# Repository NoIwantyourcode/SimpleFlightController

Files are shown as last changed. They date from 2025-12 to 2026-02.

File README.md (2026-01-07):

# Introduction
Hi!,

Welcome to my simple filght controller repository

This is a flight controller as the name suggests that is specifically designed to pilot remote controlled aircraft and provides accurate data to make flying your plane easier!,
some features I plan for to be included in the firmware are
       - 3 axis stabilization
       - altitude management

This is not a comprehensize list of features I may include and the actual firmware may have a lot more

Here are a few images of the Flight controller Schematics, PCB view and Rendered PCB view

# Schematics



# PCB view



# Rendered PCB View




# Display case (one screenshot is fitted with PCB)




NOTES TO REVIEWER:

I have had to substitute a few of components due to part shortfalls like the ICM-45686 had to substituted with the ICM-45605

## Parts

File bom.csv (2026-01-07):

Your BOM |  |  | Order Information
Component | Comment | Footprint | JLCPCB Part # | Product link | Lib Type | Qty | Source | Total Price ($)
Capacitor | 1uF | 0402 | C52923 | https://jlcpcb.com/partdetail/53938-CL05A105KA5NQNC/C52923 | Basic | 20 | 20 JLCPCB | 0.06
Capacitor | 10uF | 0402 | C15525 | https://jlcpcb.com/partdetail/16204-CL05A106MQ5NUNC/C15525 | Basic | 20 | 20 JLCPCB | 0.088
Capacitor | 44uF | 0805 | C16780 | https://jlcpcb.com/partdetail/17464-CL21A476MQYNNNE/C16780 | Basic | 8 | 8 JLCPCB | 0.2288
Capacitor | 47nF | 0201 | C505465 | https://jlcpcb.com/partdetail/YAGEO-CC0201KRX5R7BB473/C505465 | Extended | 20 | 20 JLCPCB | 0.056
Capacitor | 10uF | 0805 | C440198 | https://jlcpcb.com/partdetail/439567-GRM21BR61H106KE43L/C440198 | Basic | 8 | 8 JLCPCB | 0.4968
Capacitor | 10uF | 0603 | C19702 | https://jlcpcb.com/partdetail/20411-CL10A106KP8NNNC/C19702 | Basic | 20 | 20 JLCPCB | 0.116
Capacitor | 22uF | 0805 | C45783 | https://jlcpcb.com/partdetail/46786-CL21A226MAQNNNE/C45783 | Basic | 20 | 20 JLCPCB | 0.476
Capacitor | 100nF | 0201 | C76934 | https://jlcpcb.com/partdetail/MurataElectronics-GRM033R61A104KE15D/C76934 | Extended | 36 | 36 JLCPCB | 0.0432
Capacitor | 2.2uF | 0603 | C23630 | https://jlcpcb.com/partdetail/24366-CL10A225KO8NNNC/C23630 | Basic | 20 | 20 JLCPCB | 0.112
Capacitor | 22uF | 0402 | C415703 | https://jlcpcb.com/partdetail/408393-GRM155R60J226ME11D/C415703 | Extended | 8 | 8 JLCPCB | 0.2704
Capacitor | 20pF | 0201 | C76923 | https://jlcpcb.com/partdetail/MurataElectronics-GRM0335C1H200JA01D/C76923 | Extended | 20 | 20 JLCPCB | 0.05
Capacitor | 6.8pF | 0201 | C85916 | https://jlcpcb.com/partdetail/MurataElectronics-GRM0335C1H6R8CA01D/C85916 | Extended | 20 | 20 JLCPCB | 0.038
Capacitor | 2.2uF | 0201 | C319184 | https://jlcpcb.com/partdetail/300450-GRM033R61A225ME47D/C319184 | Extended | 20 | 20 JLCPCB | 0.204
MicroSD card | TF-01A | TF-SMD_TF-01A | C91145 | https://jlcpcb.com/partdetail/Korean_HropartsElec-TF01A/C91145 | Extended | 2 | 2 JLCPCB | 0.3512
LED | LED | 0402 | C965793 | https://jlcpcb.com/partdetail/XINGLIGHT-XL1005UGC/C965793 | Extended | 20 | 20 JLCPCB | 0.152
Battery terminal | Screw_Terminal_01x02 | TerminalBlock_Xinya_XY308-2.54-2P_1x02_P2.54mm_Horizontal | C557685 | https://jlcpcb.com/partdetail/Ningbo_Xinlaiya_Elec-XY308_2_542P/C557685 | Extended | 2 | 2 JLCPCB | 0.4658
Servo pin headers | Conn_01x03 | PinHeader_1x03_P2.54mm_Vertical | C49257 | https://jlcpcb.com/partdetail/50265-2_54_1_3P/C49257 | Extended | 10 | 10 JLCPCB | 0.169
Inductors | 1uH | L2520 | C435392 | https://jlcpcb.com/partdetail/MurataElectronics-DFE252012F_1R0MP2/C435392 | Extended | 5 | 5 JLCPCB | 0.5115
Inductors | 1.5uH | IND-SMD_L4.0-W4.0-A | C7417180 | https://jlcpcb.com/partdetail/Coilcraft-XGL4020152MEC/C7417180 | Extended | 2 | 2 JLCPCB | 2.66
Inductors | 5.6uH | IND-SMD_L3.0-W3.0 | C5120864 | https://jlcpcb.com/partdetail/CENKER-CKCS3015_5_6uHM/C5120864 | Extended | 15 | 15 JLCPCB | 0.489
Inductors | FCM1608KF-601T03 | L0603 | C141723 | https://jlcpcb.com/partdetail/TAITECH-FCM1608KF601T03/C141723 | Extended | 20 | 20 JLCPCB | 0.094
Resistors | 5.1K | 0201 | C270344 | https://jlcpcb.com/partdetail/259874-0201WMF5101TEE/C270344 | Extended | 20 | 20 JLCPCB | 0.016
Resistors | 5.23K | 0201 | C332546 | https://jlcpcb.com/partdetail/RALEC-RTT015231FTH/C332546 | Extended | 20 | 20 JLCPCB | 0.02
Resistors | 30.1K | 0201 | C273278 | https://jlcpcb.com/partdetail/YAGEO-RC0201FR0730K1L/C273278 | Extended | 20 | 20 JLCPCB | 0.02
Resistors | 383 | 0201 | C423551 | https://jlcpcb.com/partdetail/416501-0201WMF3830TEE/C423551 | Extended | 20 | 20 JLCPCB | 0.01
Resistors | 10K | 0201 | C7467266 | https://jlcpcb.com/partdetail/FOJAN-FRC0201J103TS/C7467266 | Extended | 40 | 40 JLCPCB | 0.024
Resistors | 100K | 0402 | C25741 | https://jlcpcb.com/partdetail/26484-0402WGF1003TCE/C25741 | Basic | 20 | 20 JLCPCB | 0.012
Resistors | 22.1K | 0201 | C423662 | https://jlcpcb.com/partdetail/416612-0201WMF2212TEE/C423662 | Extended | 20 | 20 JLCPCB | 0.016
Boot and Reset switch | TS-1088-AR02016 | SW-SMD_L3.9-W3.0-P4.45 | C720477 | https://jlcpcb.com/partdetail/XUNPU-TS_1088AR02016/C720477 | Basic | 8 | 8 JLCPCB | 0.3544
STM32 Chip | STM32F722RETx | LQFP-64_10x10mm_P0.5mm | C118207 | https://jlcpcb.com/partdetail/STMicroelectronics-STM32F722RET6/C118207 | Extended | 2 | 2 JLCPCB | 10.3024
Battery management IC | BQ25883RGER | VFQFPN-24_L4.0-W4.0-P0.50-BL-EP2.8 | C544362 | https://jlcpcb.com/partdetail/TexasInstruments-BQ25883RGER/C544362 | Extended | 2 | 2 JLCPCB | 9.4208
Barometric Sensor | BMP580 | LGA-10_L2.0-W2.0-P0.50-TL_BMP580 | C22391138 | https://jlcpcb.com/partdetail/BoschSensortec-BMP580/C22391138 | Extended | 2 | 2 JLCPCB | 2.1662
Buck Boost Converter | TPS63070RNMR | VQFN-HR-15_L3.0-W2.5-P0.50-BL_TPS63070RNMR | C2071354 | https://jlcpcb.com/partdetail/TexasInstruments-TPS630702RNMR/C2071354 | Extended | 2 | 2 JLCPCB | 3.432
Buck Boost converter | LMR51430 | SOT-23-6 | C5219261 | https://jlcpcb.com/partdetail/TexasInstruments-LMR51430YFDDCR/C5219261 | Extended | 2 | 2 JLCPCB | 1.813
Inertial Measurement Unit | ICM-45686 | LGA-14_L3.0-W2.5-P0.50-TL | C38673635 | https://jlcpcb.com/partdetail/TDKInvenSense-ICM45605/C38673635 | Extended | 2 | 2 JLCPCB | 14.2938
Type C port | TYPE-C16PIN2MD(073) | USB-C-SMD_TYPE-C-6PIN-2MD-073 | C2765186 | https://jlcpcb.com/partdetail/SHOUHAN-TYPE_C_16PIN_2MD_073/C2765186 | Extended | 3 | 3 JLCPCB | 0.189
Crystal | X322525MOB4SI | CRYSTAL-SMD_4P-L3.2-W2.5-BL | C9006 | https://jlcpcb.com/partdetail/YXC_CrystalOscillators-X322525MOB4SI/C9006 | Basic | 6 | 6 JLCPCB | 0.4098
Crystal | X321532768KGD2SI | OSC-SMD_L3.2-W1.5 | C620155 | https://jlcpcb.com/partdetail/649983-X321532768KGD2SI/C620155 | Extended | 5 | 5 JLCPCB | 1.0905
 |  |  |  |  |  |  | Total Price: | 50.7216
 |  |  |  |  |  |  | Other fees | 96.89
 |  |  |  |  |  |  | Total Incl. Fees and Shipping | 148.3

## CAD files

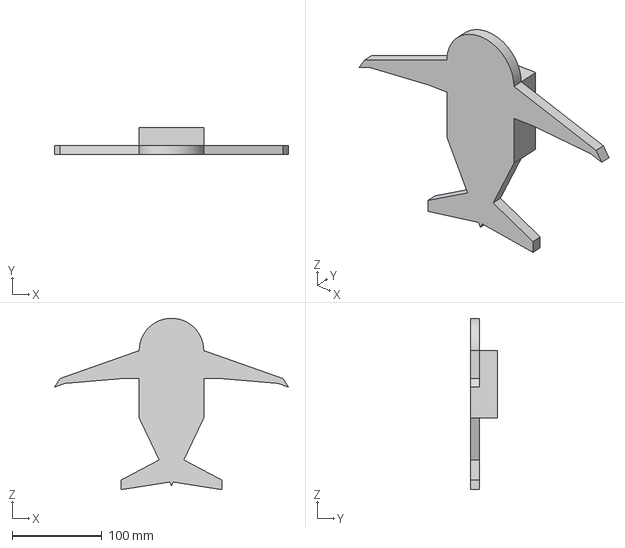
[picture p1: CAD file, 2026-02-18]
hardware/Simple flight controller case.step
260.5 x 30.0 x 190.8 mm

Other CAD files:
hardware/Simple flight controller case.f3z

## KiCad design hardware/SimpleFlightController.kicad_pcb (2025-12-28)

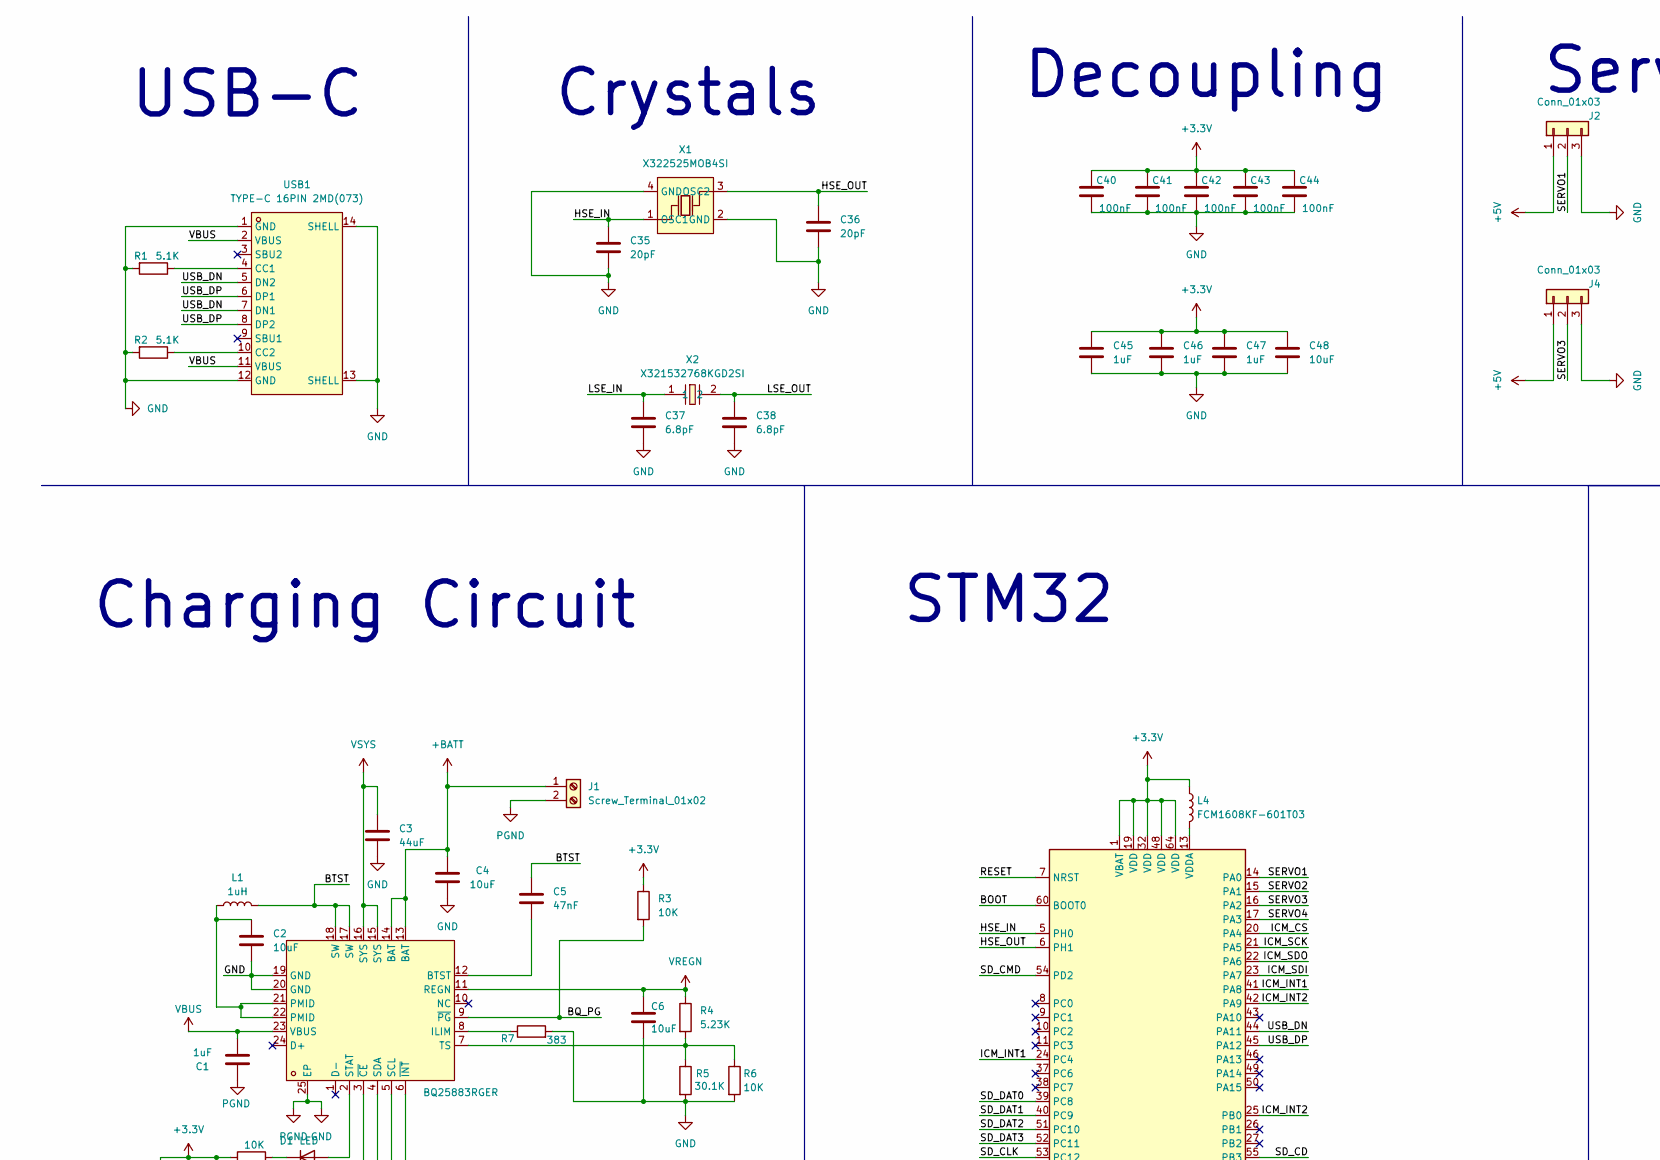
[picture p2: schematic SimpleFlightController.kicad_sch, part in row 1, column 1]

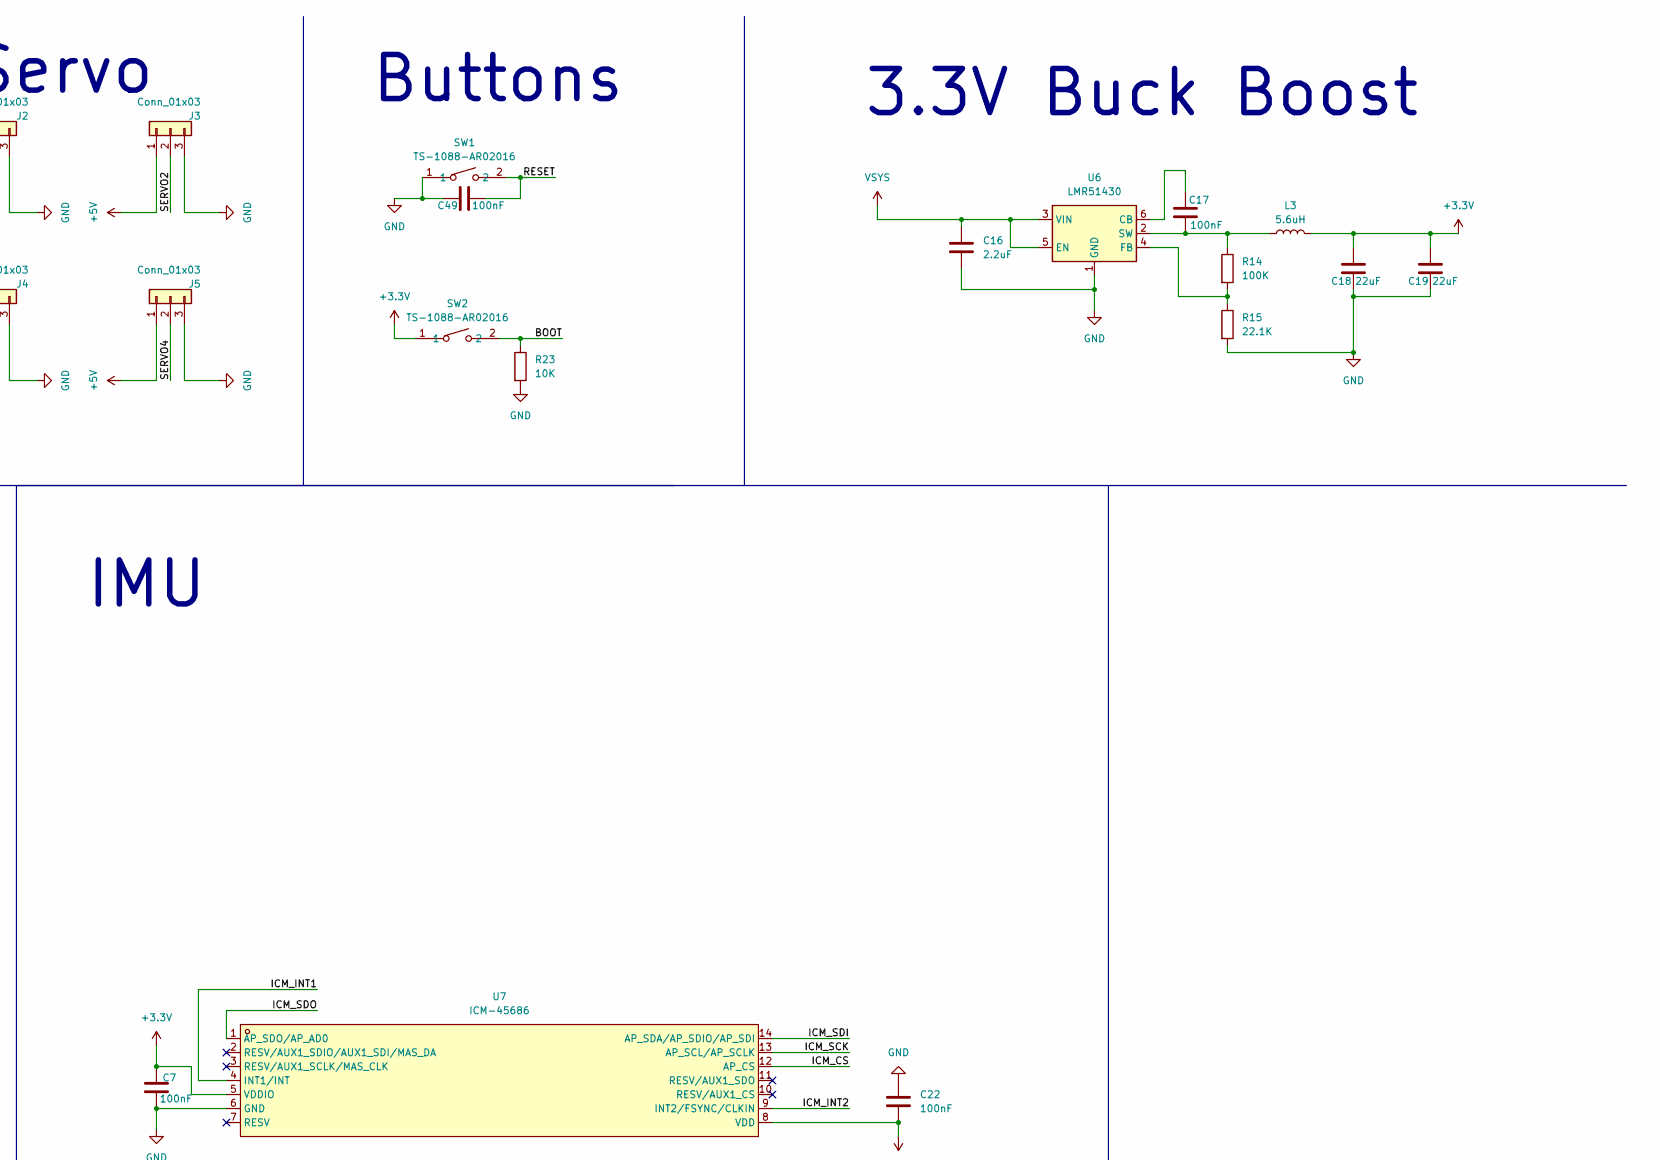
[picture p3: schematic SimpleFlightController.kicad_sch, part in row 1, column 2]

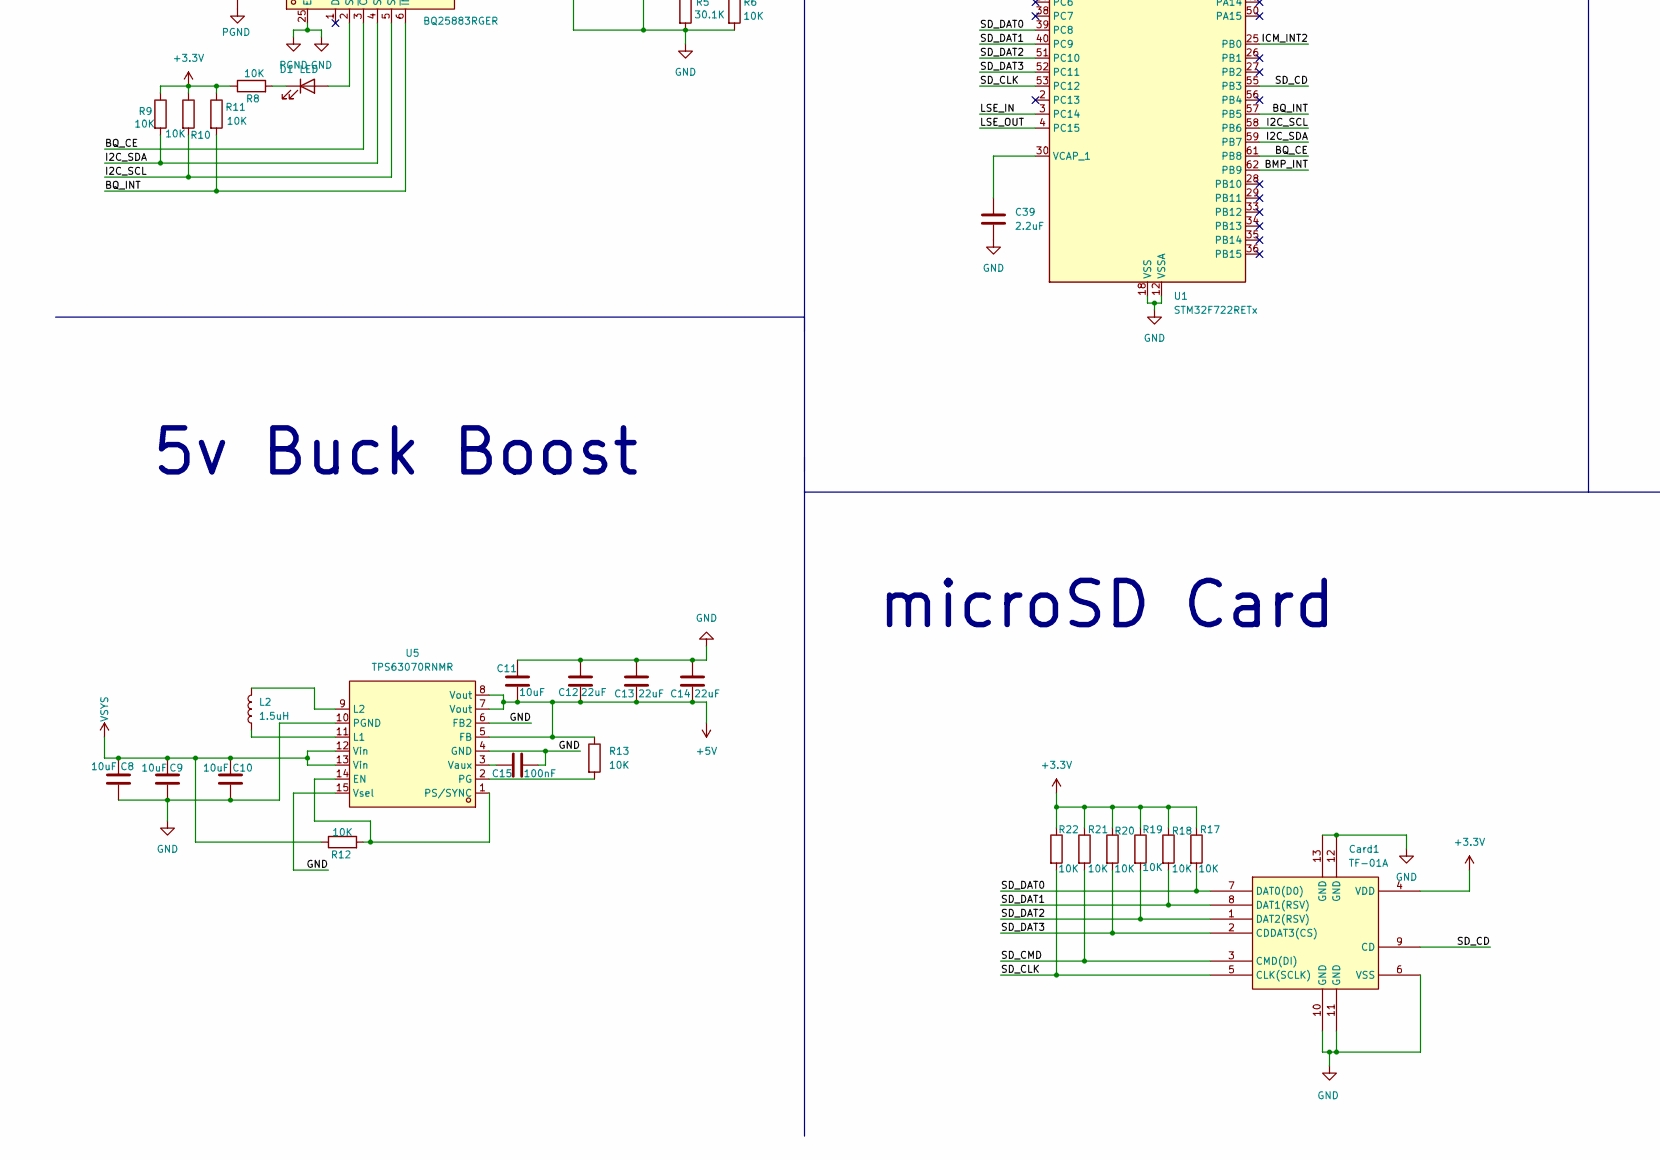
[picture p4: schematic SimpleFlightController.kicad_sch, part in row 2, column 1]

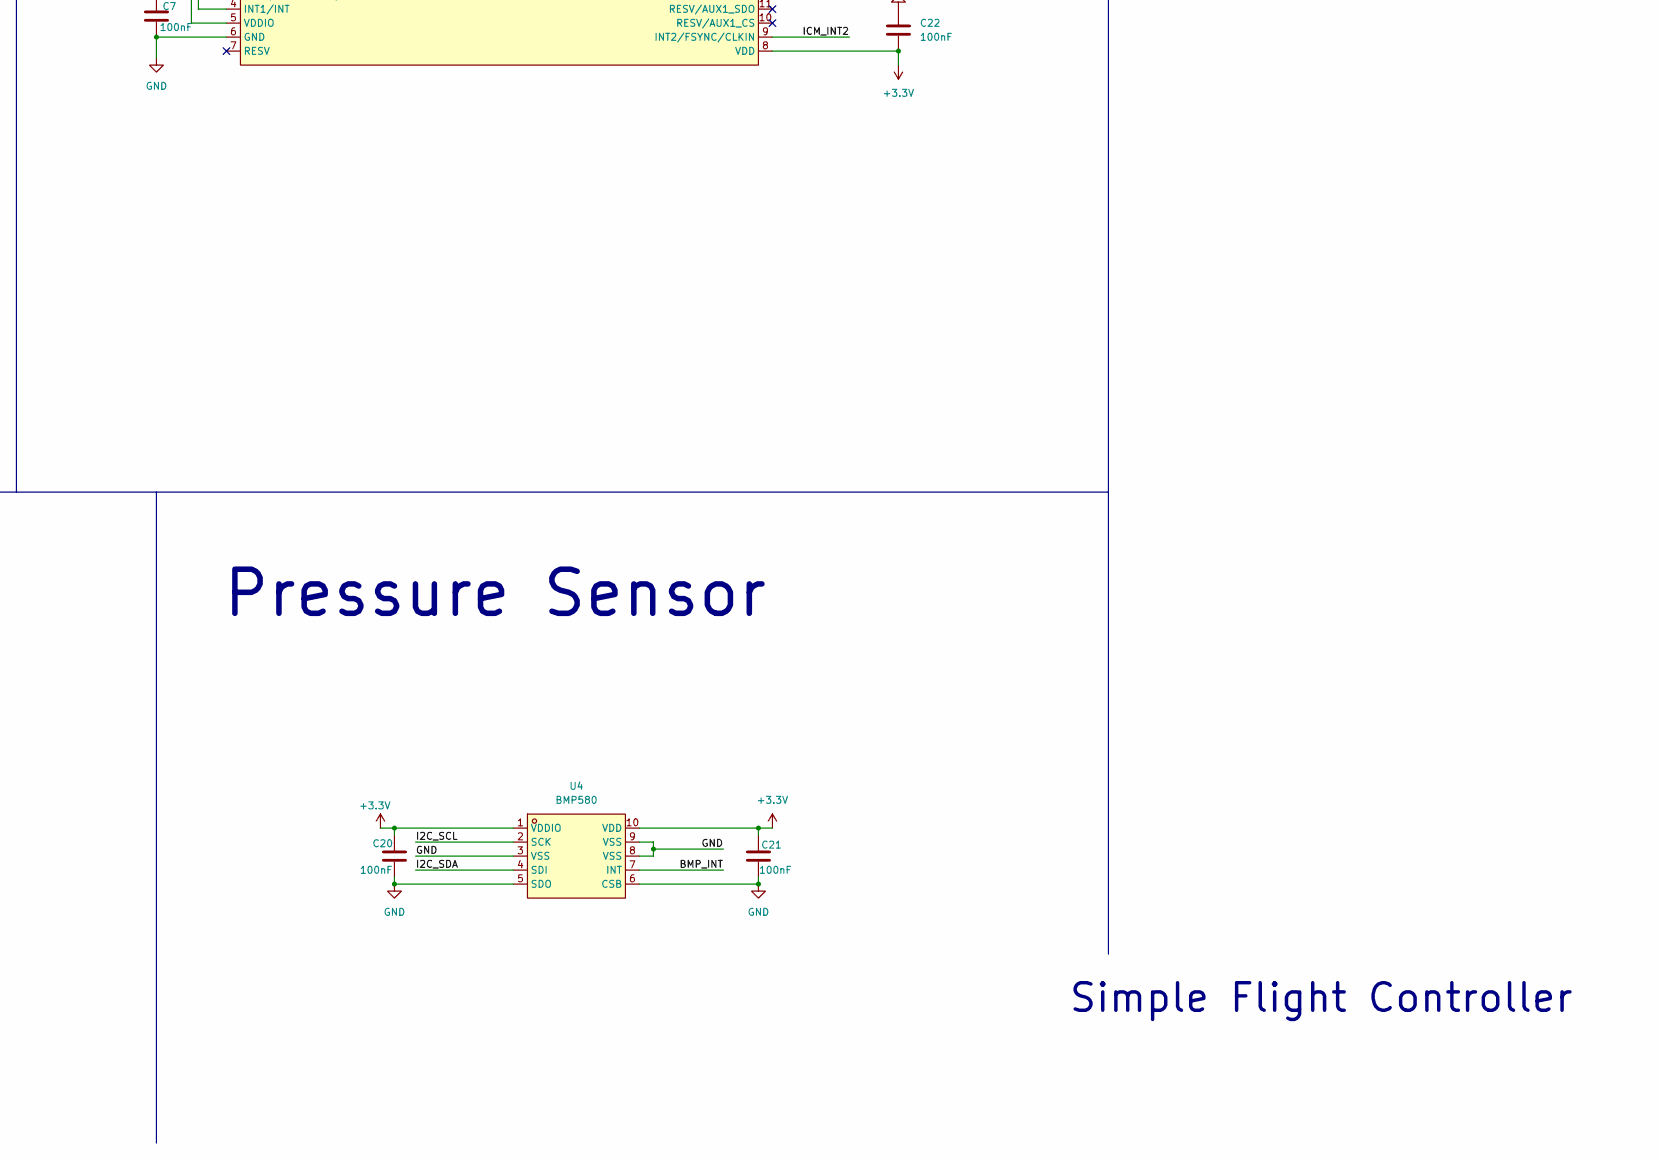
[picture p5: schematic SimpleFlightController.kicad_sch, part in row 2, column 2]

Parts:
C1, C45, C46, C47: 1uF; C_0402_1005Metric
C2, C6, C48: 10uF; C_0402_1005Metric
C3: 44uF; C_0805_2012Metric
C4, C10, C11: 10uF; C_0603_1608Metric
C5: 47nF; C_0201_0603Metric
C7, C15, C17, C20, C21, C22, C40, C41, C42, C43, C44, C49: 100nF; C_0201_0603Metric
C8, C9: 10uF; C_0805_2012Metric
C12, C13, C14: 22uF; C_0805_2012Metric
C16: 2.2uF; C_0603_1608Metric
C18, C19: 22uF; C_0402_1005Metric
C35, C36: 20pF; C_0201_0603Metric
C37, C38: 6.8pF; C_0201_0603Metric
C39: 2.2uF; C_0201_0603Metric
Card1: TF-01A; TF-SMD_TF-01A; LCSC Part C91145
D1: LED; LED_0402_1005Metric
J1: Screw_Terminal_01x02; TerminalBlock_Xinya_XY308-2.54-2P_1x02_P2.54mm_Horizontal
J2, J3, J4, J5: Conn_01x03; PinHeader_1x03_P2.54mm_Vertical
L1: 1uH; L2520
L2: 1.5uH; IND-SMD_L4.0-W4.0-A
L3: 5.6uH; IND-SMD_L3.0-W3.0
L4: FCM1608KF-601T03; L0603
R1, R2: 5.1K; R_0201_0603Metric
R3, R6, R8, R9, R10, R11, R12, R13, R17, R18, R19, R20, R21, R22, R23: 10K; R_0201_0603Metric
R4: 5.23K; R_0201_0603Metric
R5: 30.1K; R_0201_0603Metric
R7: 383; R_0201_0603Metric
R14: 100K; R_0402_1005Metric
R15: 22.1K; R_0201_0603Metric
SW1, SW2: TS-1088-AR02016; SW-SMD_L3.9-W3.0-P4.45; LCSC Part C720477
U1: STM32F722RETx; LQFP-64_10x10mm_P0.5mm
U2: BQ25883RGER; VFQFPN-24_L4.0-W4.0-P0.50-BL-EP2.8; LCSC Part C544362
U4: BMP580; LGA-10_L2.0-W2.0-P0.50-TL_BMP580; LCSC Part C22391138
U5: TPS63070RNMR; VQFN-HR-15_L3.0-W2.5-P0.50-BL_TPS63070RNMR; LCSC Part C109322
U6: LMR51430; SOT-23-6
U7: ICM-45686; LGA-14_L3.0-W2.5-P0.50-TL; LCSC Part C22459454
USB1: TYPE-C 16PIN 2MD(073); USB-C-SMD_TYPE-C-6PIN-2MD-073; LCSC Part C2765186
X1: X322525MOB4SI; CRYSTAL-SMD_4P-L3.2-W2.5-BL; LCSC Part C9006
X2: X321532768KGD2SI; OSC-SMD_L3.2-W1.5; LCSC Part C620155

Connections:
+3.3V: C7.1, C18.2, C19.2, C20.1, C21.2, C22.2, C40.1, C41.1, C42.1, C43.1, C44.1, C45.1, C46.1, C47.1, C48.1, Card1.4 (VDD), L3.2, L4.1, R3.1, R8.1, R9.1, R10.1, R11.1, R17.1, R18.1, R19.1, R20.1, R21.1, R22.1, SW2.1, U1.1 (VBAT), U1.19 (VDD), U1.32 (VDD), U1.48 (VDD), U1.64 (VDD), U4.1 (VDDIO), U4.10 (VDD), U7.5 (VDDIO), U7.8 (VDD)
+5V: C11.1, C12.1, C13.1, C14.1, J2.1, J3.1, J4.1, J5.1, R13.1, U5.5 (FB), U5.7 (Vout), U5.8 (Vout)
+BATT: C4.1, J1.1, U2.13 (BAT), U2.14 (BAT)
/BMP_INT: U1.62 (PB9), U4.7 (INT)
/BOOT: R23.1, SW2.2, U1.60 (BOOT0)
/BQ_CE: U1.61 (PB8), U2.3 (~CE)
/BQ_INT: R11.2, U1.57 (PB5), U2.6 (~INT)
/BQ_PG: R3.2, U2.9 (~PG)
/BTST: C5.1, L1.2, U2.17 (SW), U2.18 (SW)
/HSE_IN: C35.1, U1.5 (PH0), X1.1 (OSC1)
/HSE_OUT: C36.1, U1.6 (PH1), X1.3 (OSC2)
/I2C_SCL: R10.2, U1.58 (PB6), U2.5 (SCL), U4.2 (SCK)
/I2C_SDA: R9.2, U1.59 (PB7), U2.4 (SDA), U4.4 (SDI)
/ICM_CS: U1.20 (PA4), U7.12 (AP_CS)
/ICM_INT1: U1.24 (PC4), U1.41 (PA8), U7.4 (INT1/INT)
/ICM_INT2: U1.25 (PB0), U1.42 (PA9), U7.9 (INT2/FSYNC/CLKIN)
/ICM_SCK: U1.21 (PA5), U7.13 (AP_SCL/AP_SCLK)
/ICM_SDI: U1.23 (PA7), U7.14 (AP_SDA/AP_SDIO/AP_SDI)
/ICM_SDO: U1.22 (PA6), U7.1 (AP_SDO/AP_AD0)
/LSE_IN: C37.1, U1.3 (PC14), X2.1
/LSE_OUT: C38.1, U1.4 (PC15), X2.2
/RESET: C49.1, SW1.2, U1.7 (NRST)
/SD_CD: Card1.9 (CD), U1.55 (PB3)
/SD_CLK: Card1.5 (CLK(SCLK)), R22.2, U1.53 (PC12)
/SD_CMD: Card1.3 (CMD(DI)), R21.2, U1.54 (PD2)
/SD_DAT0: Card1.7 (DAT0(D0)), R17.2, U1.39 (PC8)
/SD_DAT1: Card1.8 (DAT1(RSV)), R18.2, U1.40 (PC9)
/SD_DAT2: Card1.1 (DAT2(RSV)), R19.2, U1.51 (PC10)
/SD_DAT3: Card1.2 (CDDAT3(CS)), R20.2, U1.52 (PC11)
/SERVO1: J2.2, U1.14 (PA0)
/SERVO2: J3.2, U1.15 (PA1)
/USB_DN: U1.44 (PA11), USB1.5 (DN2), USB1.7 (DN1)
/USB_DP: U1.45 (PA12), USB1.6 (DP1), USB1.8 (DP2)
GND: C1.1, C2.2, C3.2, C4.2, C6.2, C7.2, C8.2, C9.2, C10.2, C11.2, C12.2, C13.2, C14.2, C15.2, C16.2, C18.1, C19.1, C20.2, C21.1, C22.1, C35.2, C36.2, C37.2, C38.2, C39.2, C40.2, C41.2, C42.2, C43.2, C44.2, C45.2, C46.2, C47.2, C48.2, C49.2, Card1.6 (VSS), Card1.10 (GND), Card1.11 (GND), Card1.12 (GND), Card1.13 (GND), J1.2, J2.3, J3.3, J4.3, J5.3, R1.2, R2.2, R5.2, R6.2, R7.2, R15.2, R23.2, SW1.1, U1.12 (VSSA), U1.18 (VSS), U1.31 (VSS), U1.47 (VSS), U1.63 (VSS), U2.19 (GND), U2.20 (GND), U2.25 (EP), U4.3 (VSS), U4.5 (SDO), U4.6 (CSB), U4.8 (VSS), U4.9 (VSS), U5.4 (GND), U5.6 (FB2), U5.10 (PGND), U5.15 (Vsel), U6.1 (GND), U7.6 (GND), USB1.1 (GND), USB1.12 (GND), USB1.13 (SHELL), USB1.14 (SHELL), X1.2 (GND), X1.4 (GND)
unnamed: C2.1, L1.1, U2.21 (PMID), U2.22 (PMID)
unnamed: D1.2 (A), U2.2 (STAT)
unnamed: D1.1 (K), R8.2
unnamed: J4.2, U1.16 (PA2)
unnamed: J5.2, U1.17 (PA3)
unnamed: C39.1, U1.30 (VCAP_1)
unnamed: L4.2, U1.13 (VDDA)
unnamed: C5.2, U2.12 (BTST)
unnamed: R7.1, U2.8 (ILIM)
unnamed: R4.2, R5.1, R6.1, U2.7 (TS)
unnamed: R12.2, U5.1 (PS/SYNC), U5.14 (EN)
unnamed: L2.1, U5.11 (L1)
unnamed: L2.2, U5.9 (L2)
unnamed: R13.2, U5.2 (PG)
unnamed: C15.1, U5.3 (Vaux)
unnamed: C17.1, U6.6 (CB)
unnamed: R14.2, R15.1, U6.4 (FB)
unnamed: C17.2, L3.1, R14.1, U6.2 (SW)
unnamed: R1.1, USB1.4 (CC1)
unnamed: R2.1, USB1.10 (CC2)
VBUS: C1.2, U2.23 (VBUS), USB1.2 (VBUS), USB1.11 (VBUS)
VREGN: C6.1, R4.1, U2.11 (REGN)
VSYS: C3.1, C8.1, C9.1, C10.1, C16.1, R12.1, U2.15 (SYS), U2.16 (SYS), U5.12 (Vin), U5.13 (Vin), U6.3 (VIN), U6.5 (EN)

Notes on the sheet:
STM32
Crystals
Simple Flight Controller
3.3V Buck Boost
Buttons
Charging Circuit
USB-C
Decoupling
Servo
Pressure Sensor
5v Buck Boost
microSD Card
IMU

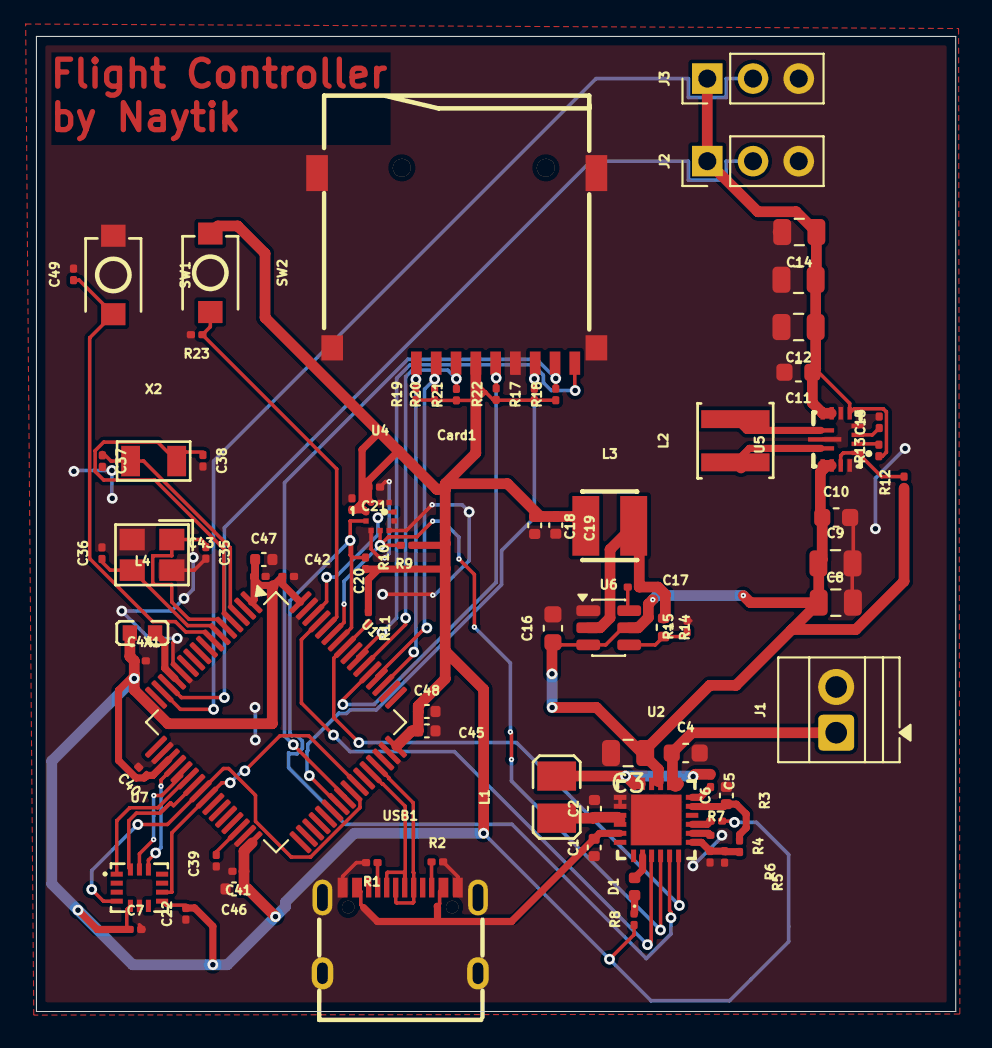
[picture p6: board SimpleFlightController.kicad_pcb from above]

Board: 2 copper layers, 51.1 x 54.2 mm, 79 parts (0 on the bottom side), 55 nets.

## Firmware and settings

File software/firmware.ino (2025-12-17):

#include <Wire.h>
#include <SPI.h>
#include <Servo.h>
#include <Adafruit_BMP5xx.h>
#include "ICM45605.h"

Adafruit_BMP5xx bmp;
ICM456xx imu(SPI, 10, 1000000); // SPI, CS pin = 10, 1 MHz (change pin number)

Servo servo1;
Servo servo2;

void setup() {
  Serial.begin(115200);
  Wire.begin();
  SPI.begin();

  // Initialize BMP580
  if (!bmp.begin(BMP5XX_DEFAULT_ADDRESS, &Wire)) {
    Serial.println("BMP580 not found!");
    while (1);
  }

  bmp.setTemperatureOversampling((bmp5xx_oversampling_t)BMP5_OVERSAMPLING_8X);
  bmp.setPressureOversampling((bmp5xx_oversampling_t)BMP5_OVERSAMPLING_4X);
  bmp.setIIRFilterCoeff((bmp5xx_iir_filter_t)BMP5_IIR_FILTER_COEFF_3);

  // Initialize IMU
  if (imu.begin() != 0) {
    Serial.println("ICM-45605 init failed!");
    while (1);
  }
  imu.startAccel(1000, 16);
  imu.startGyro(1000, 2000);

  servo1.attach(3); //change pin number
  servo2.attach(5); //change pin number

  Serial.println("Setup complete.");
}

void loop() {
  if (!bmp.performReading()) {
    Serial.println("Failed to read BMP580!");
    return;
  }
  float altitude = bmp.readAltitude(1013.25);

  inv_imu_sensor_data_t imuData;
  imu.getDataFromRegisters(imuData);

  float ax = imuData.accel_data[0];
  float ay = imuData.accel_data[1];
  float az = imuData.accel_data[2];

  float roll = atan2(ay, az) * 57.3;
  float pitch = atan2(-ax, sqrt(ay * ay + az * az)) * 57.3;

  int servo1Angle = constrain(90 + roll, 0, 180);
  int servo2Angle = constrain(90 + pitch, 0, 180);

  servo1.write(servo1Angle);
  servo2.write(servo2Angle);

  Serial.print("Alt: "); Serial.print(altitude);
  Serial.print(" Roll: "); Serial.print(roll);
  Serial.print(" Pitch: "); Serial.println(pitch);

  delay(50);
}

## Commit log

2025-12-15 These are the design files for the flight controller
    [SimpleFlightController.kicad_pcb, SimpleFlightController.kicad_sch]
2025-12-15 KiCAD design file for the Flight Controller
    [SimpleFlightController.kicad_pcb, SimpleFlightController.kicad_sch]
2025-12-16 Production files for PCBA
    Includes BOM (Bill of Materials), Component positioning files for PCB assembly and Gerber file for the board itself
    [bom.csv, designators.csv, positions.csv]
2025-12-16 firmware for the controller, uses Arduino IDE
2025-12-23 New BOM provided by JLCPCB
    [bom-JLCPCB Assembly Order.xls]
2025-12-23 Added new BOM by JLCPCB
    [bom.csv]
2025-12-23 Updated BOM
    [bom.xlsx]
2025-12-23 Updated BOM.csv
    [bomv2.csv]
2025-12-25 Other Costs for the use of PCBA in the project
2026-01-07 added project design files
    [SimpleFlightController.kicad_pcb, SimpleFlightController.kicad_sch]
2026-01-07 added Bill of Materials
    [bom.csv]
2026-01-07 added production files
    [designators.csv, positions.csv]
2026-02-18 added cad file and source file
    [Simple flight controller case.f3z, Simple flight controller case.step]
